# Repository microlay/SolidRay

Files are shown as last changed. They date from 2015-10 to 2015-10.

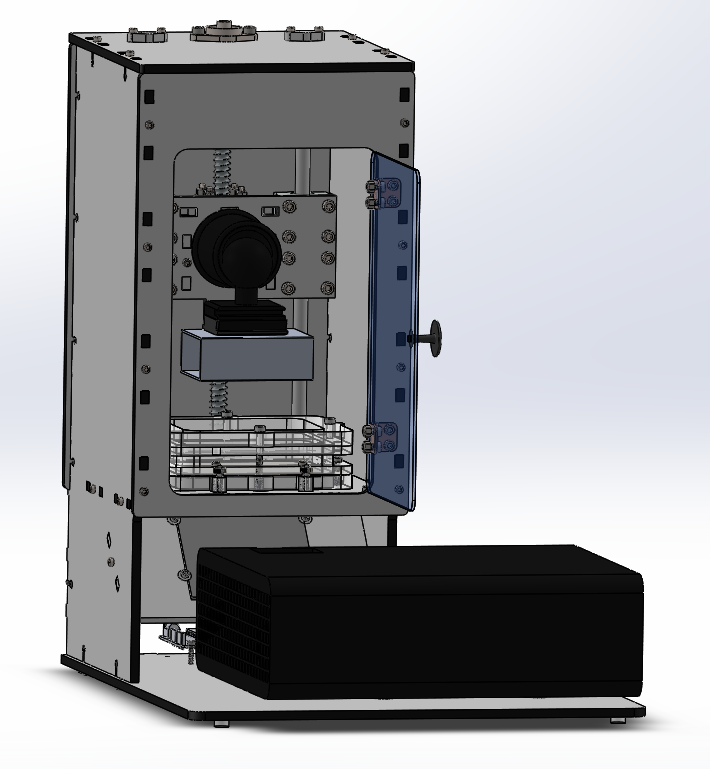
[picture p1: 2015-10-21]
SolidRay.png

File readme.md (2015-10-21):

SolidRay SLA/DLP 3D printer kit
====

Explore the limits of High Definition 3D Printing
----

SolidRay is a stereolithographic 3D printer kit based on DLP technology developed by  [kitprinter3D](http://solidray.kitprinter3d.com). for those seeking an introduction to high definition 3D printing.

License 
----

Solidray by [kitprinter3D](http://solidray.kitprinter3d.com) is licensed under a [Creative Commons Attribution-NonCommercial-ShareAlike 4.0 International License](http://creativecommons.org/licenses/by-nc-sa/4.0/)

Assembly:
-----------
The full assembly manual is hosted and updated at our webpage: http://www.kitprinter3d.com/en/blog/solidray-assembly-manual-c12

BOM:
-----------
- Electronics:
  - 1x Acer P1500 DLP Projector (STL/STEP)
  - 1x Arduino UNO (STL/STEP)
  - 1x CNC 3.0
  - 1x A4988 Stepper controller
  - 1x NEMA 17
- Laser cut:
  - 6mm melamine
    - 1x Melamine base
    - 1x melamine mirror support
    - 2x melamine sides
    - 1x back upper cover
    - 1x front upper cover
    - 1x FlexVAT base 1
    - 1x FlexVAT base 2
    - 1x Base Z_Lift
    - 2x Framing square
    - 1x Ballscrew nut holder
    - 1x Top cover
    - 2x Rod cover
  - 2mm acrylic
    - 1x FEP Holder
    - 1x FlexVAT floor
  - 3mm acrylic (coloured if desired)
    - 1x electronics cover
    - 1x anti UV front door
  - 6mm acrylic
    - 1x FlexVAT layer 2
    - 1x FlexVAT layer 3
  - 10mm acrylic
    - 1x FlexVAT layer 1
    - 1x FlexVAT layer 4
  - 20mm acrylic
    - 1x FlexVAT wall
  - 8mm rubber
    - 1x Rubber spacer FlexVAT
  - Screws & common hardware
    - 3x Nylon spacer
    - 6x DIN912 M3x12 screws
    - 57x DIN912 M3x16 screws
    - 3x DIN912 M3x30 **or** M4x30 screws (P1500 adaptor)
    - 3x M3 **or** M4 washer (P1500 adaptor)
    - 6x M3 nylon washer
    - 40x M3 nut
    - 12x M3 locknut
    - 4x M3x40 capscrew
    - 4x M3 thumbscrew
    - 4x DIN 912 M4x8 screws
    - 4x DIN 912 M4x12 screws
    - 4x DIN 912 M4x20 screws
    - 4x DIN912 M4x35 screws
    - 12x M4 locknut
    - 18x DIN 912 M5x12 screws
    - 4x grower washer
    - 1x M10 washer
    - 1x 3/8” x 1/2” screw
  - 1x 90x90mm first surface mirror
  - 1x Z-coupling
  - 8x M3 brass insert
  - 4x M4 brass insert
  - 4x SC10UU bearings
  - 1x Beike Bk-03 Ballhead
  - 1x Printing base
  - 1x Ballscrew antibacklash nut
  - 2x M10x306 rod
  - 2x hinges
  - 1x Knob
  - 6x adhesive legs
  - 3x P1500 adaptor (3D printed)

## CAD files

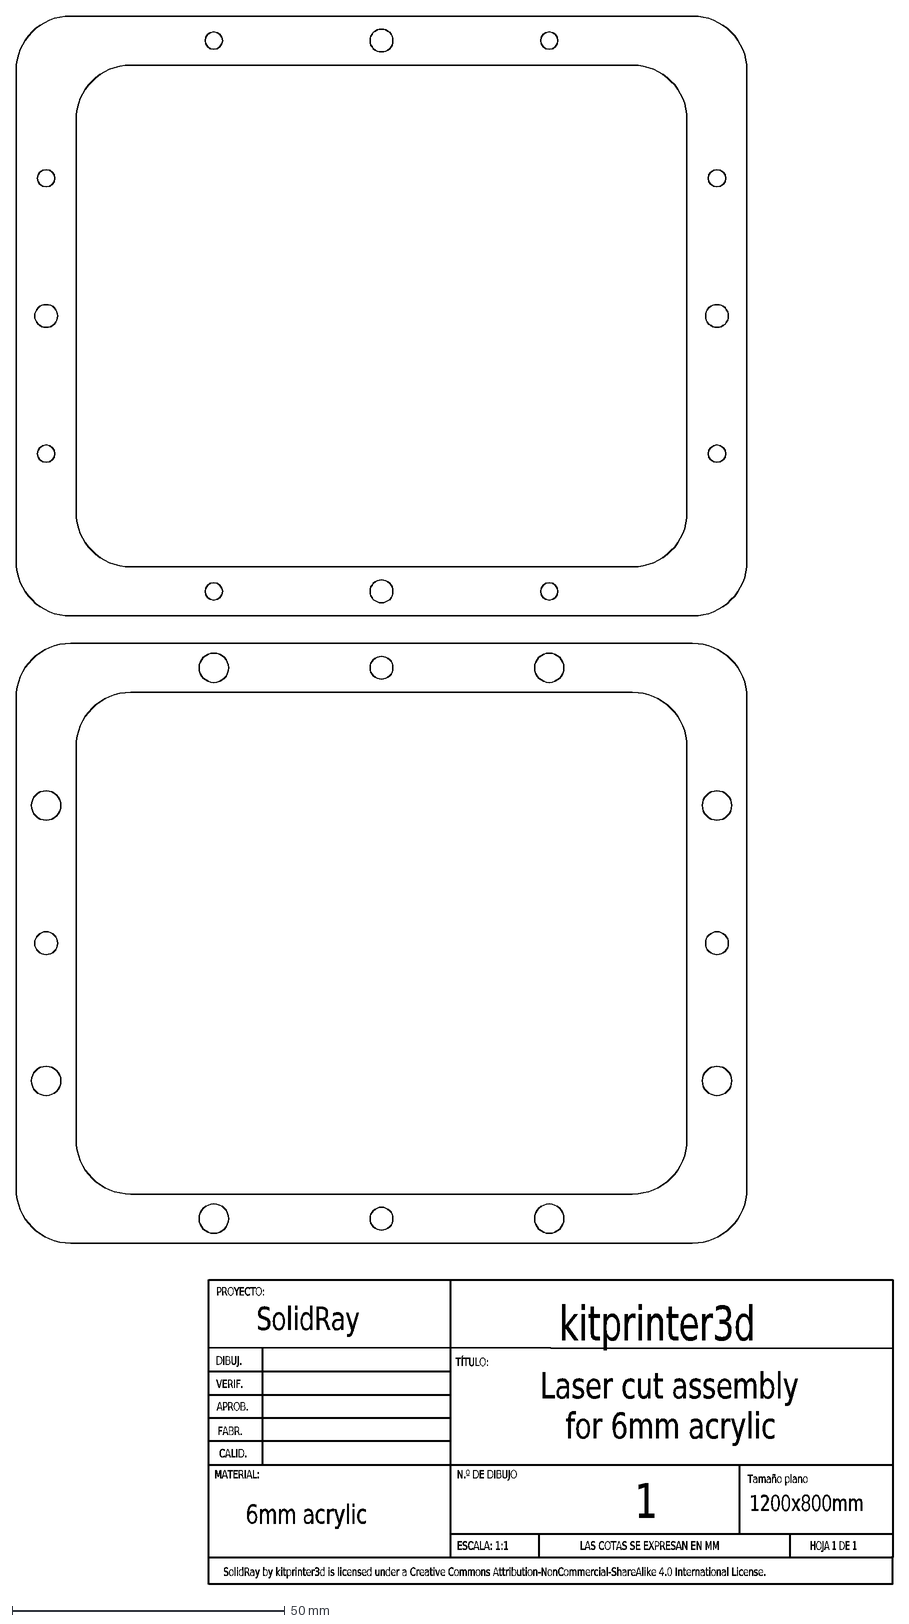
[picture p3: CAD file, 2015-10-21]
dxf/6mm acrylic laser cut assembly.DXF
6mm acrylic
Laser cut assembly
for 6mm acrylic
Tamaño plano
DIBUJ.
VERIF.
APROB.
FABR.
CALID.
LAS COTAS SE EXPRESAN EN MM
PROYECTO:
MATERIAL:
TÍTULO:
N.º DE DIBUJO
ESCALA: 1:1
HOJA 1 DE 1
1200x800mm
1
SolidRay by kitprinter3d is licensed under a Creative Commons Attribution-NonCommercial-ShareAlike 4.0 International License.
SolidRay
kitprinter3d

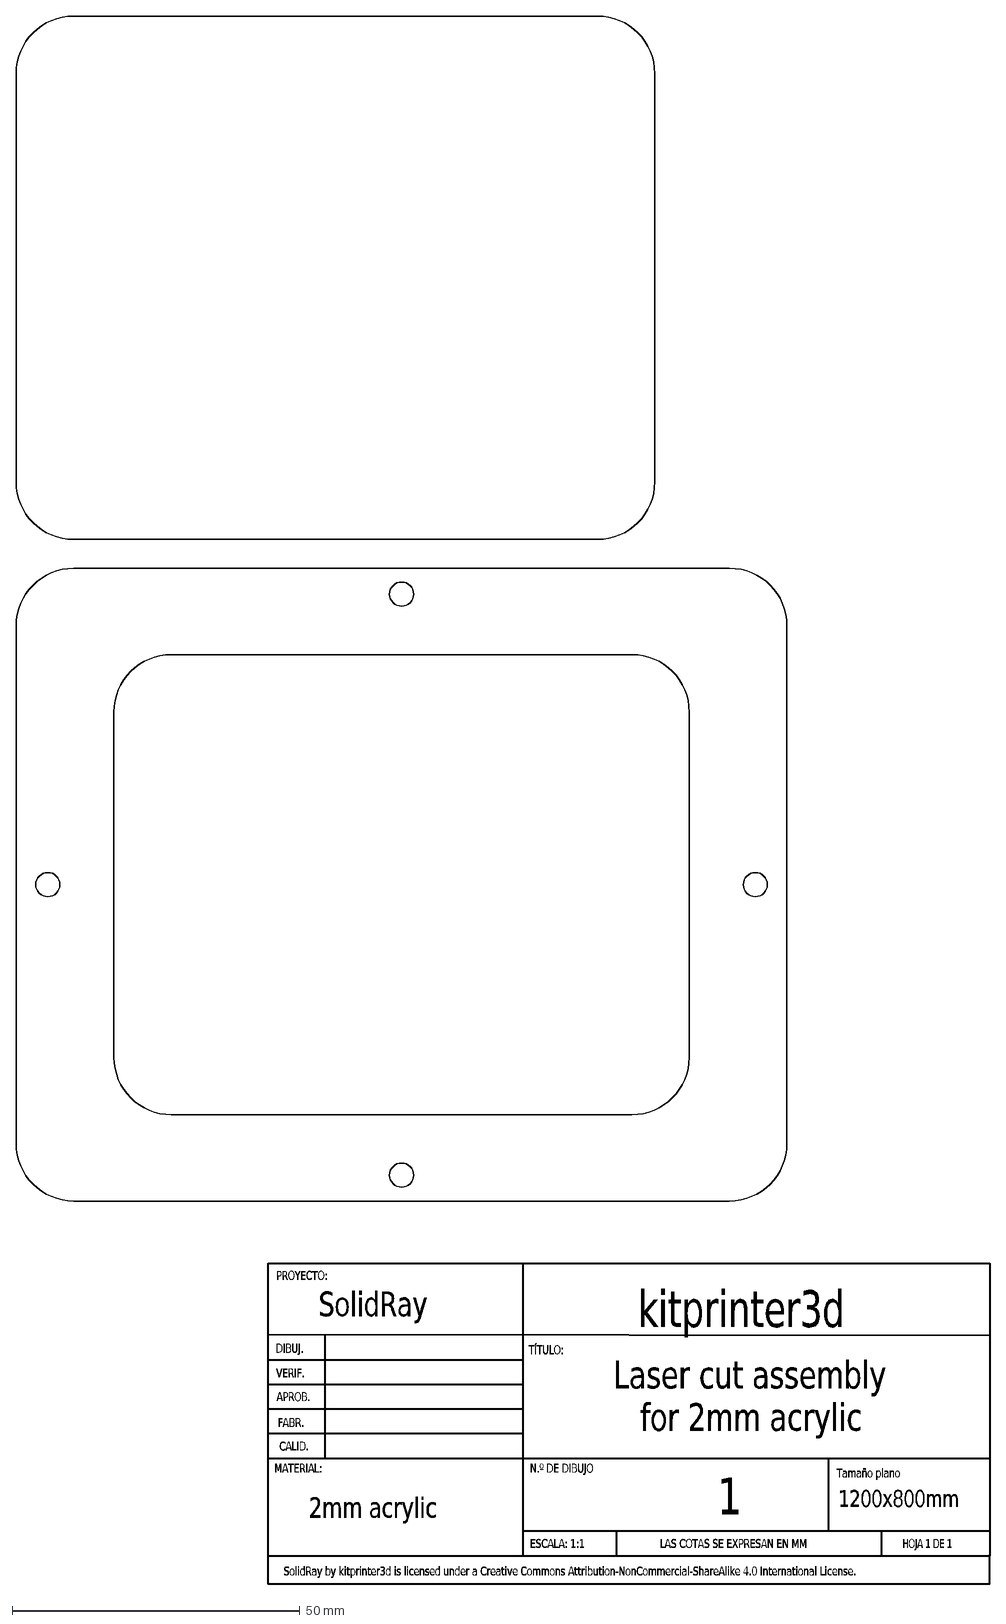
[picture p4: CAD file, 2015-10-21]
dxf/2mm acrylic laser cut assembly.DXF
2mm acrylic
Laser cut assembly
for 2mm acrylic
Tamaño plano
DIBUJ.
VERIF.
APROB.
FABR.
CALID.
LAS COTAS SE EXPRESAN EN MM
PROYECTO:
MATERIAL:
TÍTULO:
N.º DE DIBUJO
ESCALA: 1:1
HOJA 1 DE 1
1200x800mm
1
SolidRay by kitprinter3d is licensed under a Creative Commons Attribution-NonCommercial-ShareAlike 4.0 International License.
SolidRay
kitprinter3d

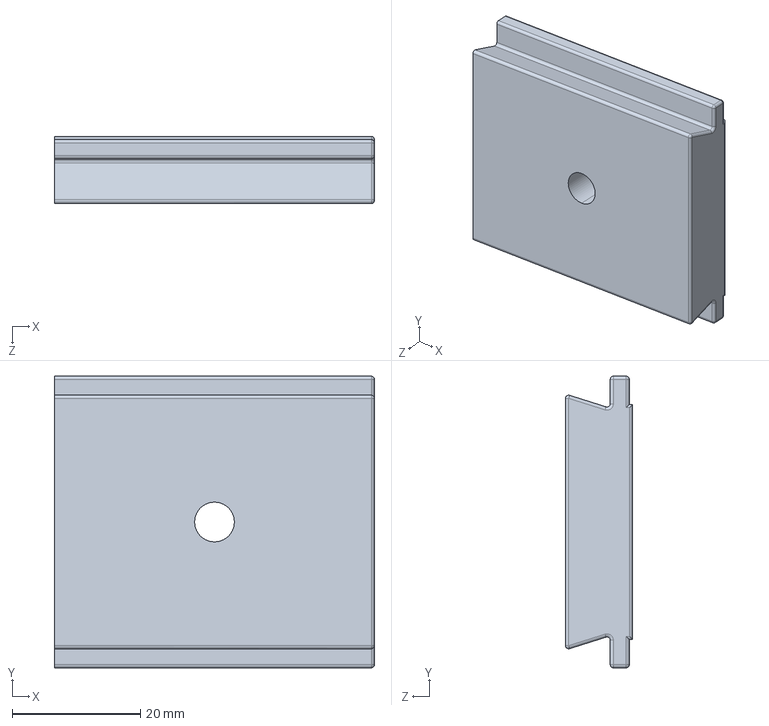
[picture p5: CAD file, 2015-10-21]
step/Beike Bk-03 quick release.STEP
50.0 x 45.6 x 10.5 mm

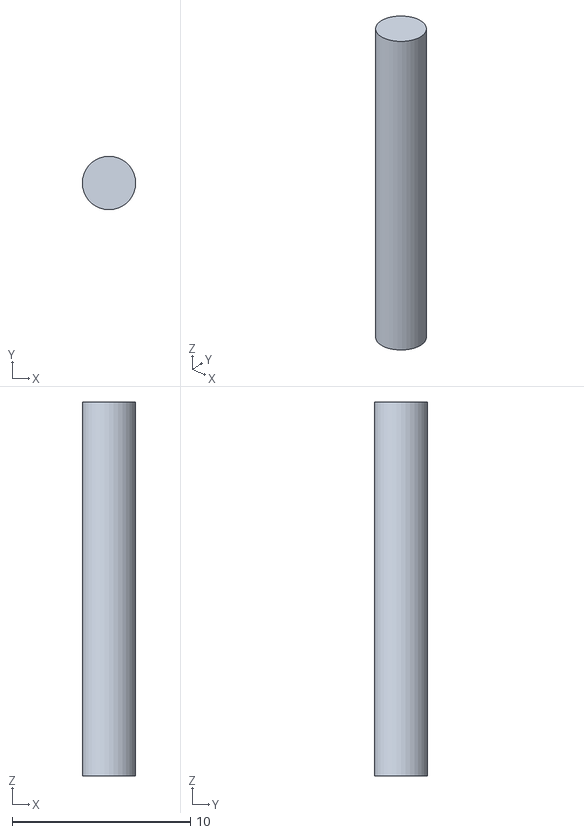
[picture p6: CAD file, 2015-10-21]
stl/Hinge pin.SLDPRT.STL
3.00 x 3.00 x 21.0

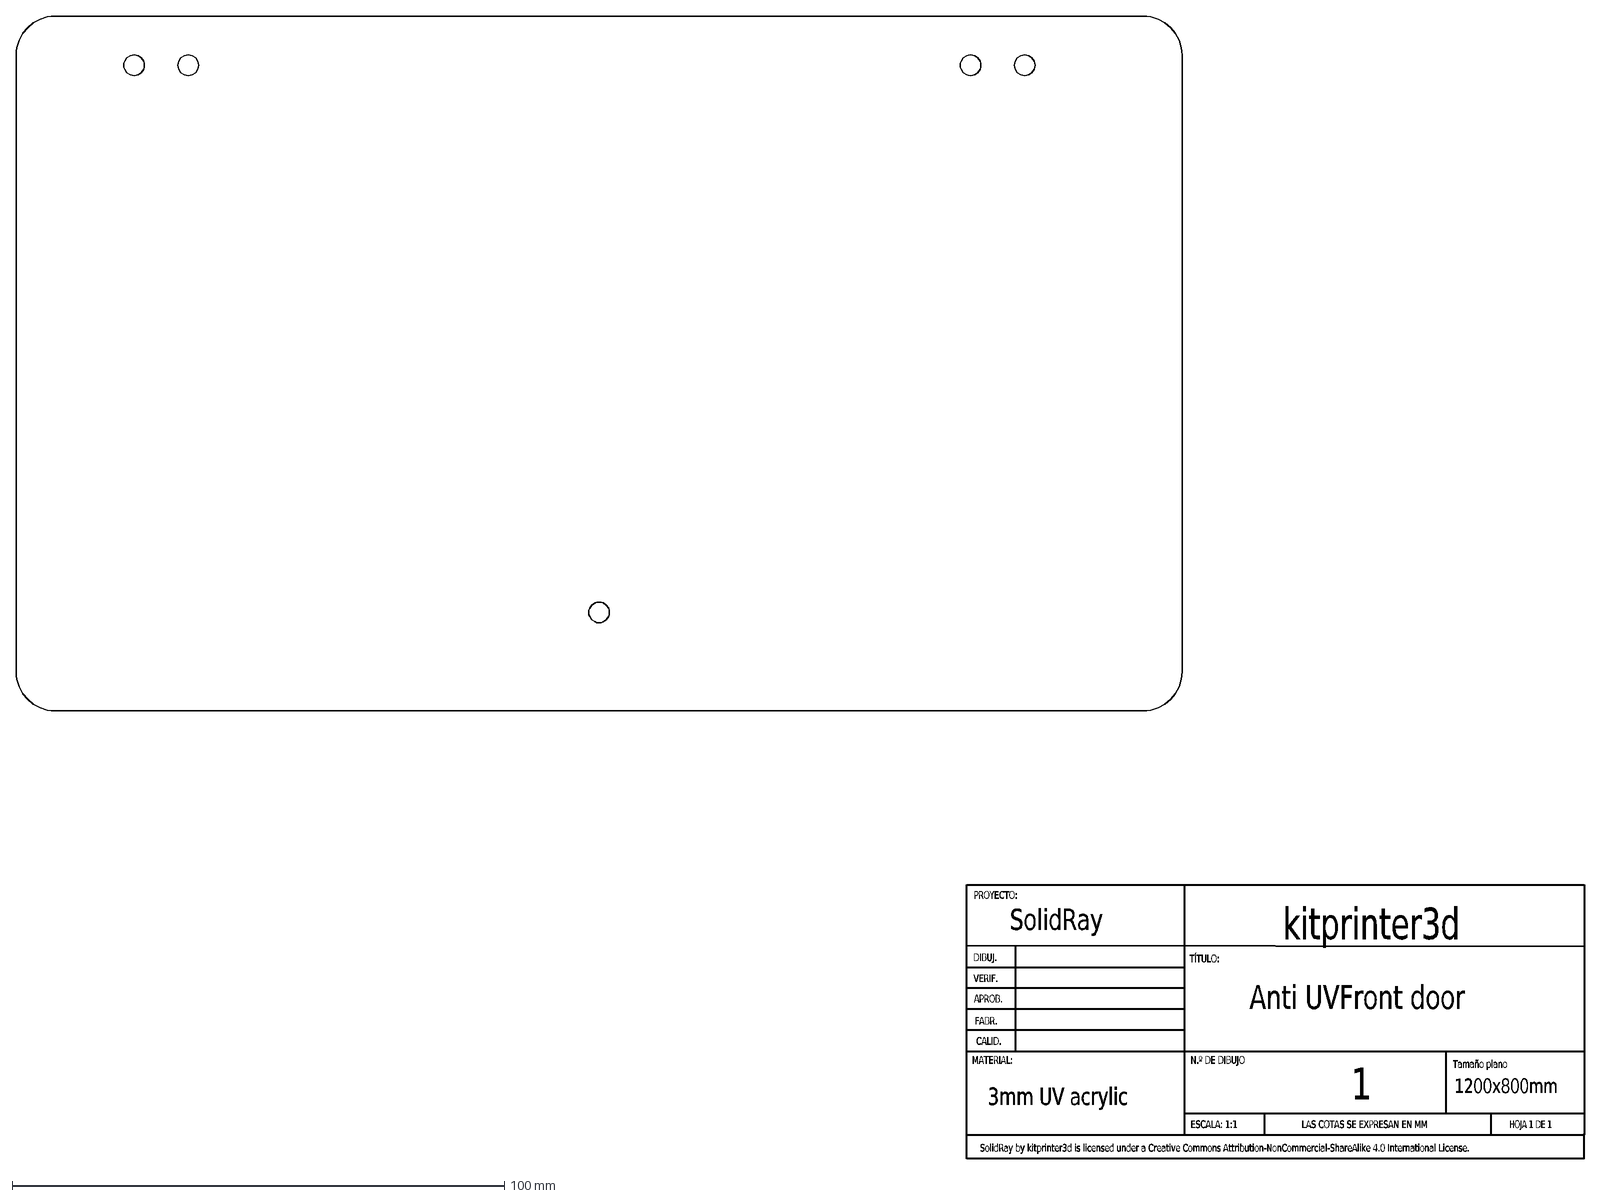
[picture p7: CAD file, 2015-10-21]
dxf/AntiUV front door.DXF
3mm UV acrylic
Anti UVFront door
Tamaño plano
DIBUJ.
VERIF.
APROB.
FABR.
CALID.
LAS COTAS SE EXPRESAN EN MM
PROYECTO:
MATERIAL:
TÍTULO:
N.º DE DIBUJO
ESCALA: 1:1
HOJA 1 DE 1
1200x800mm
1
SolidRay by kitprinter3d is licensed under a Creative Commons Attribution-NonCommercial-ShareAlike 4.0 International License.
SolidRay
kitprinter3d

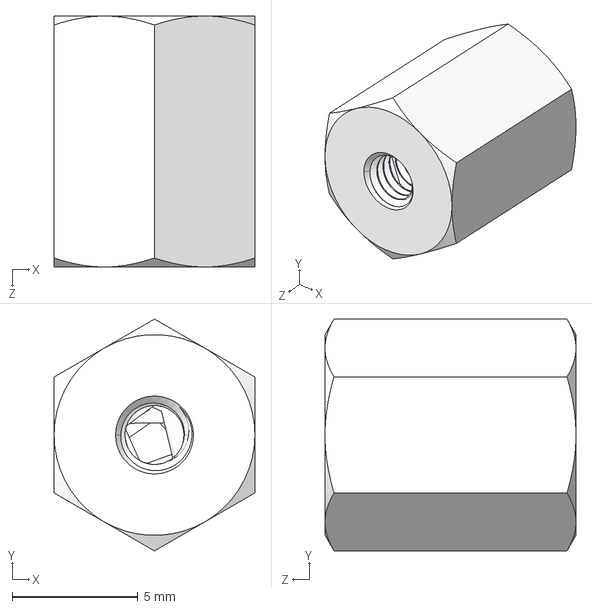
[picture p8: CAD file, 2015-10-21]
step/Nylon spacer.STEP
8.00 x 9.24 x 10.0 mm

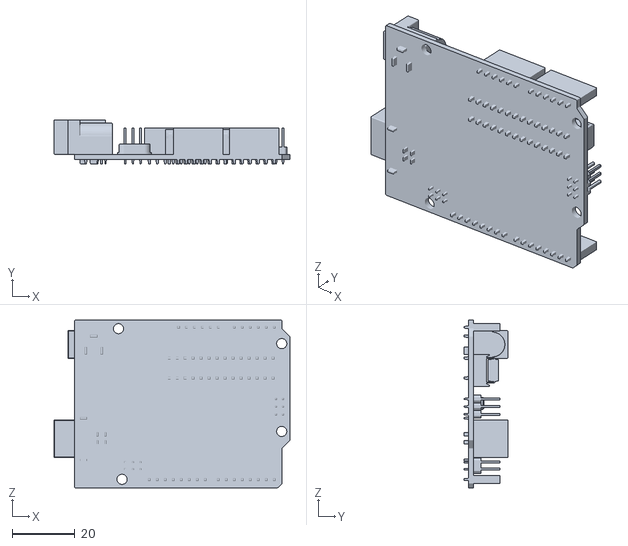
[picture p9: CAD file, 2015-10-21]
stl/Arduino UNO.STL
75.1 x 14.0 x 53.3

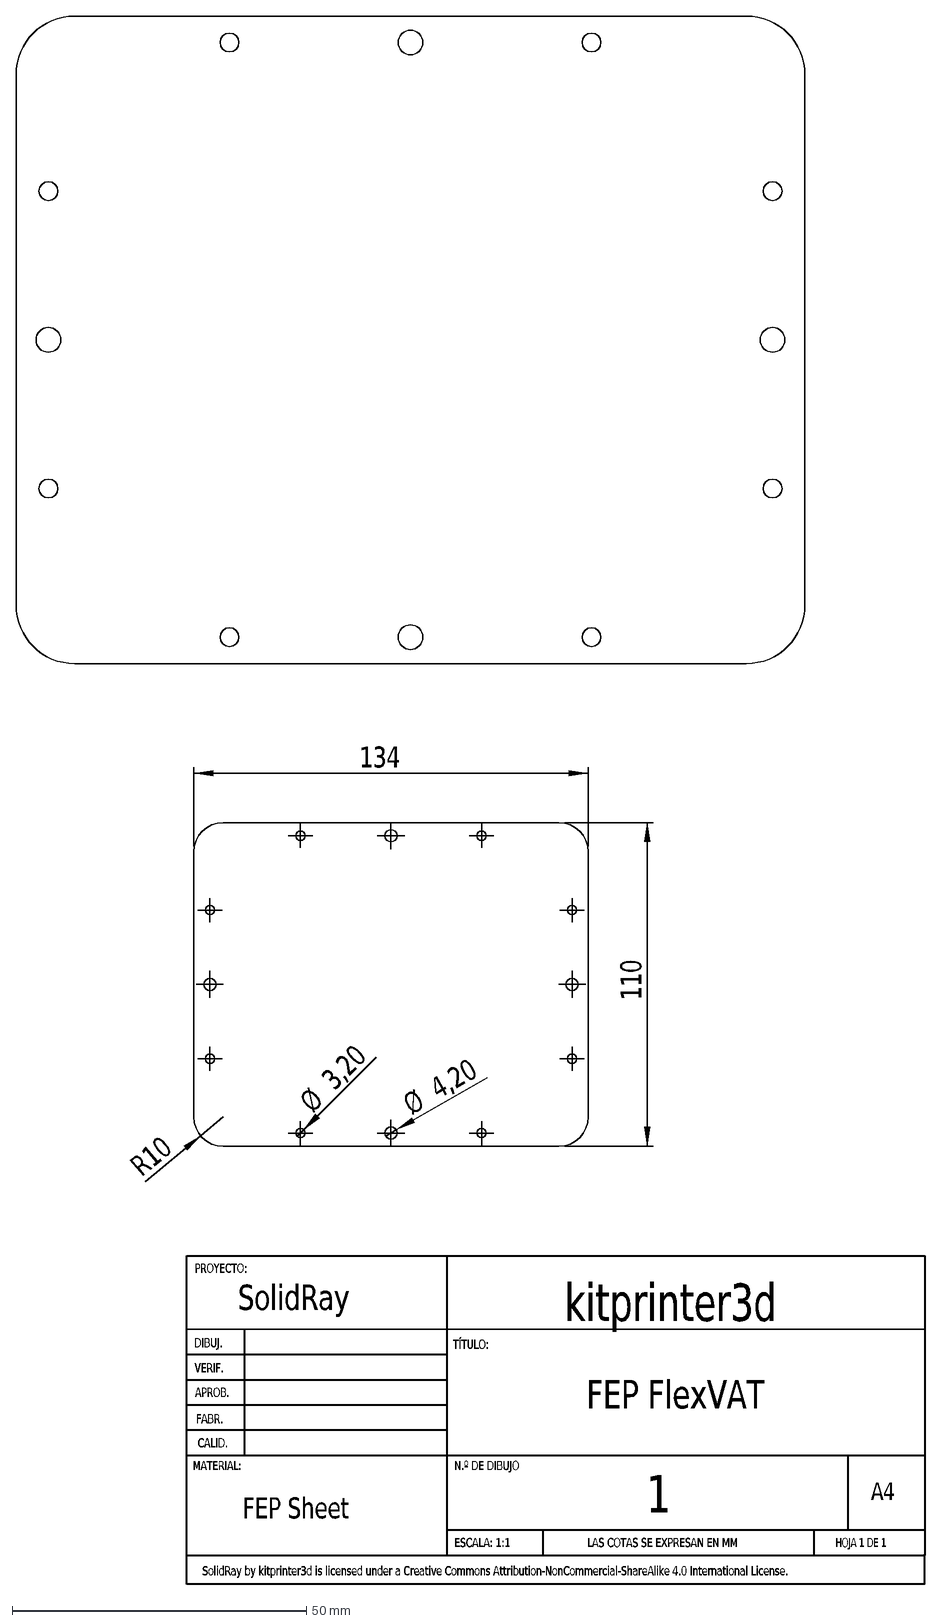
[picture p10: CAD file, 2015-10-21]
dxf/FEP sheet.DXF
FEP Sheet
FEP FlexVAT
kitprinter3d
SolidRay
SolidRay by kitprinter3d is licensed under a Creative Commons Attribution-NonCommercial-ShareAlike 4.0 International License.
1
A4
HOJA 1 DE 1
ESCALA: 1:1
N.º DE DIBUJO
TÍTULO:
MATERIAL:
PROYECTO:
LAS COTAS SE EXPRESAN EN MM
CALID.
FABR.
APROB.
VERIF.
DIBUJ.
134
110
R10
Ø
4,20
3,20

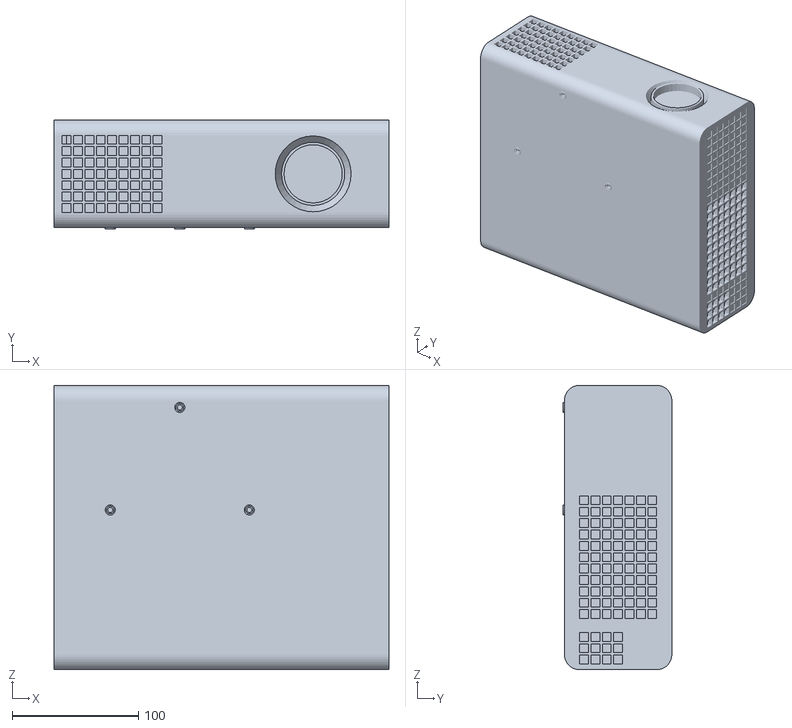
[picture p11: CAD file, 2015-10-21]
stl/Acer P1500 DLP projector.STL
265.0 x 86.0 x 225.0

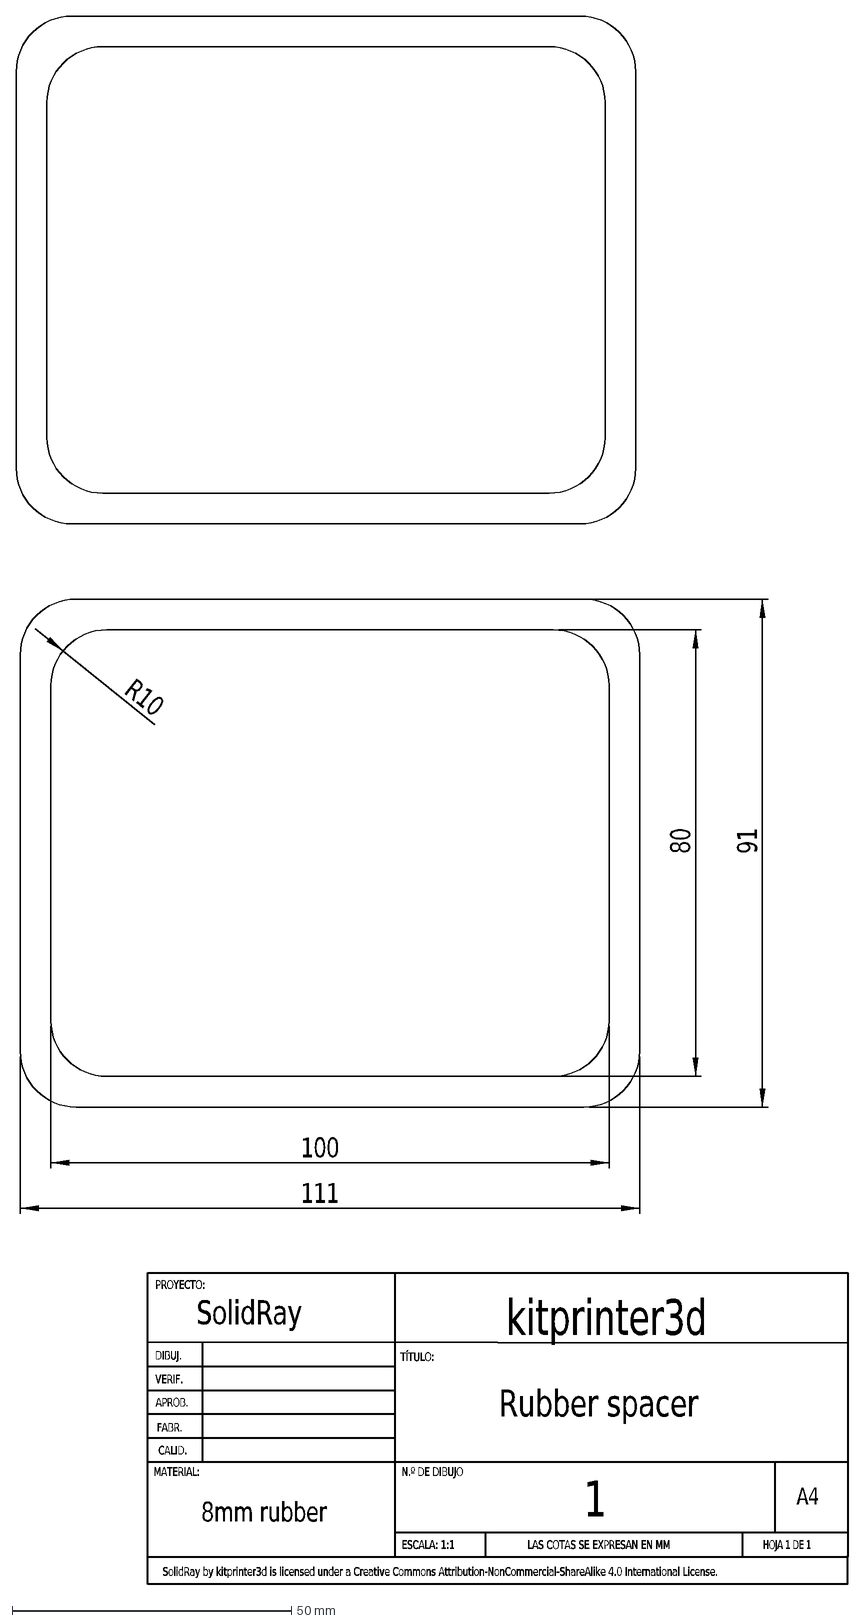
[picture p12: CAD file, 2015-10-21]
dxf/Rubber Spacer.DXF
8mm rubber
Rubber spacer
DIBUJ.
VERIF.
APROB.
FABR.
CALID.
LAS COTAS SE EXPRESAN EN MM
PROYECTO:
MATERIAL:
TÍTULO:
N.º DE DIBUJO
ESCALA: 1:1
HOJA 1 DE 1
A4
1
SolidRay by kitprinter3d is licensed under a Creative Commons Attribution-NonCommercial-ShareAlike 4.0 International License.
SolidRay
kitprinter3d
111
100
91
80
R10

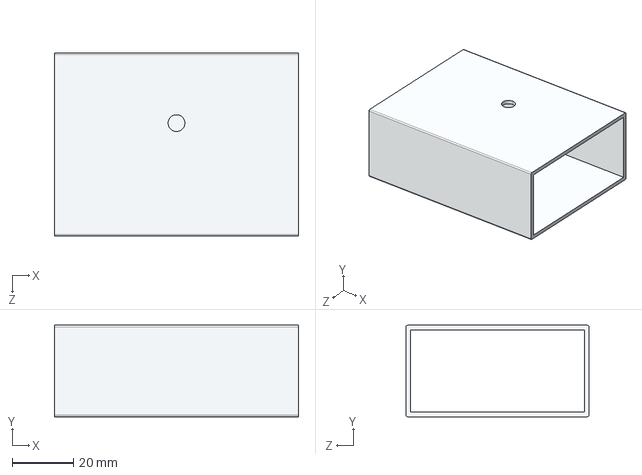
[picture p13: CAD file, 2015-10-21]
step/Printing base.STEP
80.0 x 30.0 x 60.0 mm

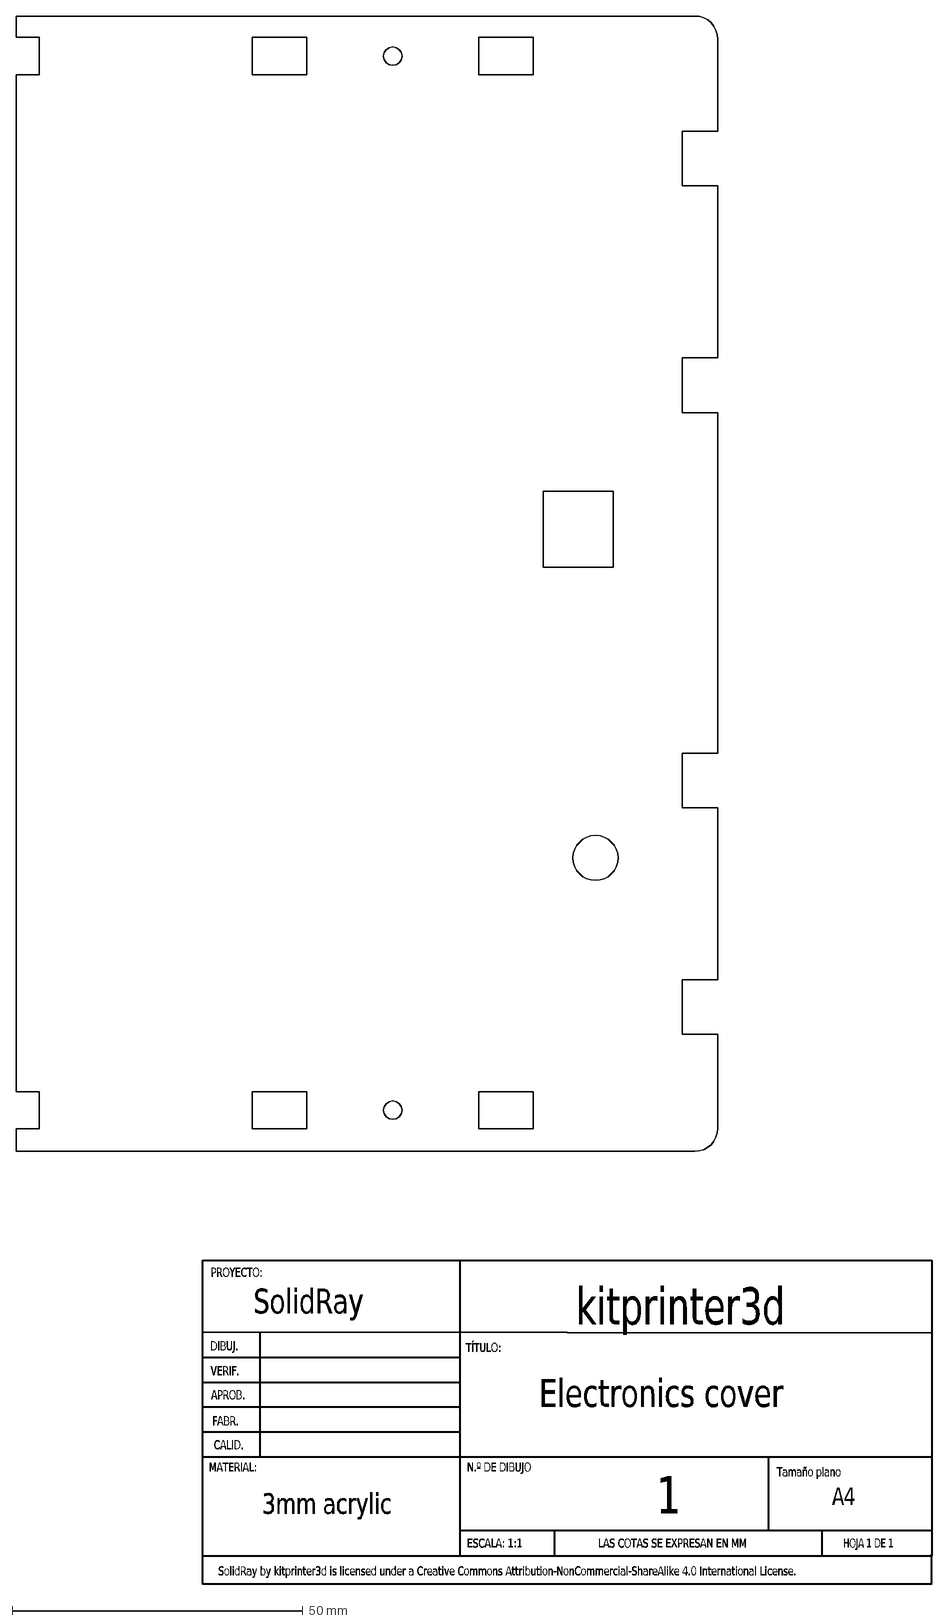
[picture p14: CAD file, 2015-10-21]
dxf/Electronics cover.DXF
3mm acrylic
Electronics cover
Tamaño plano
DIBUJ.
VERIF.
APROB.
FABR.
CALID.
LAS COTAS SE EXPRESAN EN MM
PROYECTO:
MATERIAL:
TÍTULO:
N.º DE DIBUJO
ESCALA: 1:1
HOJA 1 DE 1
A4
1
SolidRay by kitprinter3d is licensed under a Creative Commons Attribution-NonCommercial-ShareAlike 4.0 International License.
SolidRay
kitprinter3d

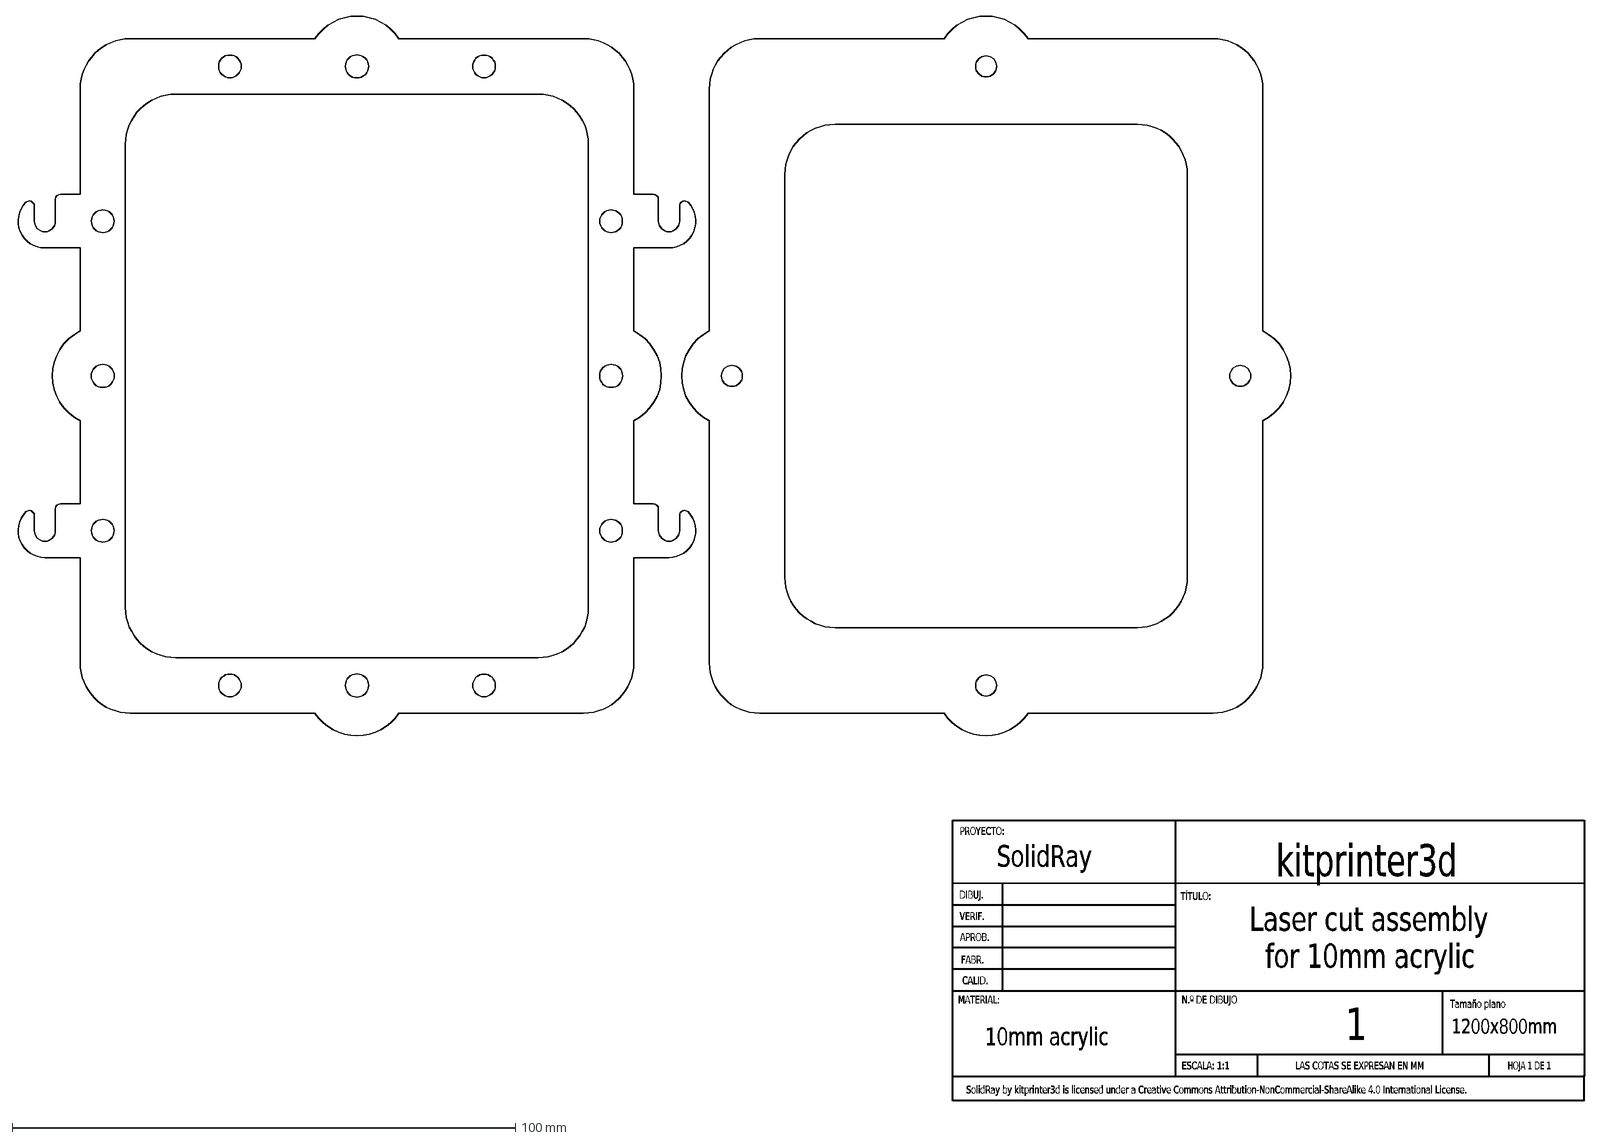
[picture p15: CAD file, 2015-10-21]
dxf/10mm acrylic.DXF
10mm acrylic
Laser cut assembly
for 10mm acrylic
Tamaño plano
DIBUJ.
VERIF.
APROB.
FABR.
CALID.
LAS COTAS SE EXPRESAN EN MM
PROYECTO:
MATERIAL:
TÍTULO:
N.º DE DIBUJO
ESCALA: 1:1
HOJA 1 DE 1
1200x800mm
1
SolidRay by kitprinter3d is licensed under a Creative Commons Attribution-NonCommercial-ShareAlike 4.0 International License.
SolidRay
kitprinter3d

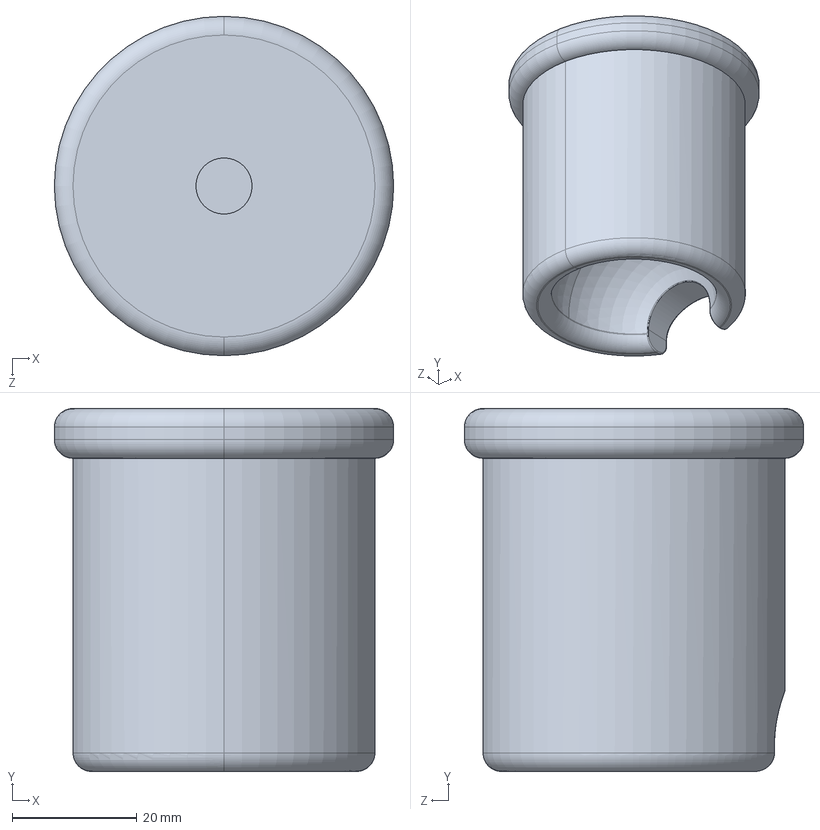
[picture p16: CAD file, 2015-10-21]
step/Beike Bk-03 fixed part.STEP
54.5 x 58.3 x 54.5 mm

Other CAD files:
dxf/6mm melamine laser cut assembly.DXF
step/Hinge.STEP
step/First surface mirror.STEP
step/Knob.STEP
step/1204 Ballscrew.STEP
step/3-8x1-2in screw detailed.STEP
step/3-8x1-2in screw.STEP
step/Adhesive legs.STEP
step/Ballscrew antibacklash nut.STEP
step/Beike Bk-03 floating part.STEP
step/DIN 912 M3x12 screw detailed.STEP
step/DIN 912 M3x12 screw.STEP
step/DIN 912 M3x16 screw detailed.STEP
step/DIN 912 M3x16 screw.STEP
step/DIN 912 M3x30 screw detailed.STEP
step/DIN 912 M3x30 screw.STEP
step/DIN 912 M4x12 screw detailed.STEP
step/DIN 912 M4x12 screw.STEP
step/DIN 912 M4x20 screw detailed.STEP
step/DIN 912 M4x20 screw.STEP
step/DIN 912 M4x35 screw detailed.STEP
step/DIN 912 M4x35 screw.STEP
step/DIN 912 M4x8 screw detailed.STEP
step/DIN 912 M4x8 screw.STEP
step/DIN 912 M5x12 screw detailed.STEP
step/DIN 912 M5x12 screw.STEP
step/Grower washer.STEP
step/Hinge pin.STEP
step/M10 washer.STEP
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
